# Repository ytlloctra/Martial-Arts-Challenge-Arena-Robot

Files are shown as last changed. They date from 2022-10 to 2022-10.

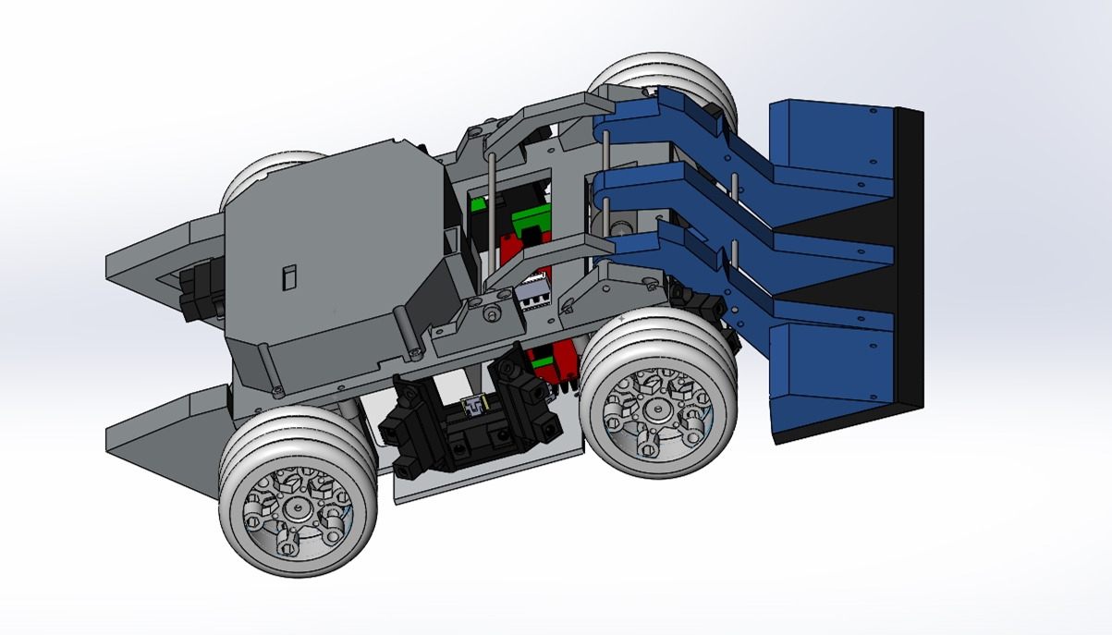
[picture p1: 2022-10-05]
3D图纸/003平铲车-改/预览图.jpg

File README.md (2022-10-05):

# 武术擂台机器人

stm32f103vet6 + oled + 得科电机 + 驼峰胎 + 红外测距传感器

## 接线

接线

传感器

Left00接PD7 

Right00接PD2

Left01接PA4

Right01接PA3

Left02接PA6

Right02接PA1

Left03接PA7

Right03接PA0

Left04接PC4

Right04接PC3 

Left05接PC5  

Right05接PC2 

Behind00接PC0

驱动板

左侧：

pwml1接PA9，pwml2接PA8，EN不接，两个GND中，只需将其中任意一个GND与主控板GND相连

右侧：

pwml1接PA11，pwml2接PA10，EN不接，两个GND中，只需将其中任意一个GND与主控板GND相连

平避障 逆时针 距离变小 顺时针 距离变大  棕正蓝负黑信号

红外测距  红正黑负黄信号

左转 左后右前  右转 左前右后

## 避障序号

避障序号

## 主要程序



```cython
void bianyuanshibie() 
{
	//int b;
if(ltsbflag==0)
{

if(hui3==1&&hui4==1&&hui1==1&&hui2==1&&mm1==1&&mm2==1)  stop();
//else ahead(300);
else if(((temp1>1700&&temp7>1700)||(temp4>1700&&temp6>1700)||(temp1>1700&&(temp4>1700||temp6>1700))||(temp7>1700&&(temp4>1700||temp6>1700))||(temp3>1700&&temp4>1700&&temp9>1700)||(temp5>1700&&temp6>1700&&temp8>1700))&&ot<3)
	{
		
			//ltsbflag=1;
					ot++;
			
	}
//else if(backflag==1&&temp1>1600) 
//{
	//if(temp1<1600) backflag=0;
	//else  stop();
//}
	
else	
{

		if(mm1==1||mm2==1||hui1==1||hui2==1)

{

	 if( temp1>1600  )    // two sensor front find enemy 2  
			{		

					if ((hui1==1||hui2==1)) 
				{
					if(temp7>1600) {left(800);x0++;}
					else	
					{
							//back(600,600);
						//if(hui1==0&&hui2==0)
						back(500,500);
						
						f++;
					}
					
				}
				
					else 
					{
						if(backflag==0)
						{
						allahead(500);
						allaheadflag=1;
						}
					}

			}
			else if(temp7>1600)  
			{
					left(800);
					x5++;
			}
		else if(  temp3>1600||temp4>1600||mm3==0||temp9>1600) //one sensor  right and right back  find enemy  and right back   2   temp3>1500 || temp4>1500  ||
			{
				
					if(temp3>1600)  right(600);
				else if(temp9>1600) right(800);
					else right(700);

			}
		else if( temp6>1600||temp5>1600||mm4==0||temp8>1600 )  //onr sensor left and left back find enemy 2    temp5>1500 ||temp6>1500 ||
			{
			
					if(temp5>1600)	left(600);
				else if(temp8>1600) left(800);
					else left(700);
				//x1++;
				
			}
		//else if(temp7>1700)  {left(720);x5++;}

		else	if(hui3==1&&hui4==1)
	{
				if(mm1==1||mm2==1||hui1==1||hui2==1)
		{
			 
				diaotou(500);x2++;
			
		}
				else
		{
		ahead(450);
		//ltsbflag=0;
		}
	}
		else 
	{
				if((hui1==1||hui2==1)&&(mm1==1||mm2==1)) {back(500,500);f++;}
				else 
				diaotou(500);
				x3++;
	}

}

else if( temp1>1600  )    // two sensor front find enemy 2  
			{		

							if(temp7>1600)  {diaotou(500);x4++;}
							else           
							{ 
						     if(backflag==0)
										{
											allahead(600);
											allaheadflag=1;
										}
							}

			}
else if(temp7>1600)  {left(900);x7++;}

else if(  temp3>1600||temp4>1600||mm3==0||temp9>1600) //one sensor  right and right back  find enemy  and right back   2   temp3>1500 || temp4>1500  ||
			{
					if(temp3>1600)  right(600);
				else if(temp9>1600) right(800);
					else right(700);
				
			}
else if( temp6>1600||temp5>1600||mm4==0||temp8>1600 )  //onr sensor left and left back find enemy 2    temp5>1500 ||temp6>1500 ||
			{
					
					if(temp5>1600)	left(600);
				else if(temp8>1600) left(800);
					else left(700);
				x6++;
			}

//else if(temp7>2000)  {left(720);x7++;}
else ahead(450);
			
}
		
}

duojiz(900);
duojiy(900);

//if(j>0&&f>0) 
	//{
 //   backflag=1;
//	}  
//	else backflag=0;
if(allaheadflag==1) 
{
	j+=4;
	if(j>300) j=300;
}
else j=0;

if(ot>2) 	{ltsbflag=1;}

}
```

## 实车



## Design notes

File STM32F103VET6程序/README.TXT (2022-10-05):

实验器材:
	MiniSTM32F103开发板V3版本
	
实验目的:
	学习定时器的PWM功能
	
硬件资源:
	1,DS0(连接在PA8) 
	2,定时器1(TIM1),使用TIM1的通道1(CH1),开启部分重映射,将TIM1_CH1输出到PA8.
	从而实现PWM输出控制DS0亮度.
	
实验现象:
	本实验,DS0由暗到亮,再由亮到暗,再由暗到亮,依次循环.
	
注意事项:
	无.  

					正点原子@ALIENTEK
					2014-3-06
					广州市星翼电子科技有限公司
					电话：020-38271790
					传真：020-36773971
					购买：http://shop62103354.taobao.com
					http://shop62057469.taobao.com
					公司网站：www.alientek.com
					技术论坛：www.openedv.com

void bianyuanshibie() 
{
	//int b;
if(ltsbflag==0)
{

if(hui3==1&&hui4==1&&hui1==1&&hui2==1&&mm1==1&&mm2==1)  stop();
//else ahead(300);
else if(((temp1>1700&&temp7>1700)||(temp4>1700&&temp6>1700)||(temp1>1700&&(temp4>1700||temp6>1700))||(temp7>1700&&(temp4>1700||temp6>1700))||(temp3>1700&&temp4>1700&&temp9>1700)||(temp5>1700&&temp6>1700&&temp8>1700))&&ot<3)
	{
		
			//ltsbflag=1;
					ot++;
			
	}
//else if(backflag==1&&temp1>1600) 
//{
	//if(temp1<1600) backflag=0;
	//else  stop();
//}
	
else	
{

		if(mm1==1||mm2==1||hui1==1||hui2==1)

{

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

		else	if(hui3==1&&hui4==1)
	{
				if(mm1==1||mm2==1||hui1==1||hui2==1)
		{
			 
				diaotou(500);x2++;
			
		}
				else
		{
		ahead(450);
		//ltsbflag=0;
		}
	}
		else 
	{
				if((hui1==1||hui2==1)&&(mm1==1||mm2==1)) {back(500,500);f++;}
				else 
				diaotou(500);
				x3++;
	}

}

else if( temp1>1600  )    // two sensor front find enemy 2  
			{		

							if(temp7>1600)  {diaotou(500);x4++;}
							else           
							{ 
						     if(backflag==0)
										{
											allahead(600);
											allaheadflag=1;
										}
							}

			}
else if(temp7>1600)  {left(900);x7++;}

else if(  temp3>1600||temp4>1600||mm3==0||temp9>1600) //one sensor  right and right back  find enemy  and right back   2   temp3>1500 || temp4>1500  ||
			{
					if(temp3>1600)  right(600);
				else if(temp9>1600) right(800);
					else right(700);
				
			}
else if( temp6>1600||temp5>1600||mm4==0||temp8>1600 )  //onr sensor left and left back find enemy 2    temp5>1500 ||temp6>1500 ||
			{
					
					if(temp5>1600)	left(600);
				else if(temp8>1600) left(800);
					else left(700);
				x6++;
			}

//else if(temp7>2000)  {left(720);x7++;}
else ahead(450);
			
}
		
}

duojiz(900);
duojiy(900);

//if(j>0&&f>0) 
	//{
 //   backflag=1;
//	}  
//	else backflag=0;
if(allaheadflag==1) 
{
	j+=4;
	if(j>300) j=300;
}
else j=0;

if(ot>2) 	{ltsbflag=1;}

}

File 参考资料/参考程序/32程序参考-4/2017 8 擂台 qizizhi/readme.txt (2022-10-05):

本实验为新建工程实验，仅供大家新建工程时参考。

	嵌入式开发网
      mcudev.taobao.com

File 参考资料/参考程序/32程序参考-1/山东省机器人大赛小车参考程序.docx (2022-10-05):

#include "delay.h"

#include "sys.h"

#include "oled.h"

#include "pwm.h"

#include "delay.h"

#include "adc.h"

#include "move.h"

#include "scan.h"

#include "buzzer.h"

//#include "usart.h"

//#include "MPU6050.h"

//#include "usmart.h"

//#include "inv_mpu.h"

#include "dma.h"

#include "timer.h"

//#include "inv_mpu_dmp_motion_driver.h"

#define TEST 0 //1为测试，0为不测试

void ltsb(void);

void delay(int t);

void TIM3_IRQHandler(void); //TIM3中断

void DMA1_Channel1_IRQHandler(void);

void bianyuanshibiex(void);

void check(void);

void show(void);

void set_num(void);

char huodejianzhi();

u8 set_led(u8 a);

extern u32 GROUP;

extern unsigned char zheng_or_fan;

extern int time;

u32 temp_z1=0,temp_z2=0,temp_z3=0,temp_z4=0,temp_z5=0,temp_z6=0,temp_y1=0,temp_y2=0,temp_y3=0,temp_y4=0,temp_y5=0,temp_y6=0,temp_Qz=0,temp_Hz=0;

u32 temp0o=0,temp1o=0,temp2o=0,temp3o=0,temp4o=0,temp5o=0,temp6o=0,temp7o=0,temp8o=0,temp9o=0,temp_left_aheado=0,temp_left_backo=0;

u8 hui1,hui2,hui3,hui4,rlfalg=1,hui5,hui6;

u8 mm1,mm2,mm3,mm4,mm5,mm6,oldmm3,oldmm4,mm7,mm8,key=0,key_flag=0;

u8 ltsbflag=0,allaheadflag=0,backflag=0,ltsbback=0,ltsbjiao=0,rightflag=0,leftflag=0,backflag1=0,backflag2=0,leitaichu=0,ltxback=0,ltxahead=0,ltsbin=0,enemyflag=0,uptai=0;

u32 xr=0,ra=0,la=0,yj=0,zj=0, t=0,ot=0,ot1=0,j=0,f=0,x=0,rf=0,lf=0,tj=0;

int x1,x2,x3,x4,x5,x6,x7,x0,sum[6]={0},mpu[6]={0},sub[6]={0},i,xj=0;

u16 value[14],y=0;

int kp=5,kd=1,lasttime=0,apwm=0,expectspeed=0,error=0,key_num=0;

u32 check45_PWM=900,check90_PWM=900,check45_TIME=100,check90_TIME=200,checkback_PWM=700,checkback_TIME=200; //check参数设置

int main(void)

{

delay_init(); //延时函数初始化

delay_ms(1000);

delay_ms(1000);

NVIC_Configuration(); //设置NVIC中断分组2:2位抢占优先级，2位响应优先级 LED_Init(); //LED端口初始化

BUZZER_GPIO_Config(); //

OLED_Init(); //初始化OLED

MYDMA_Config(DMA1_Channel1,(u32)&ADC1->DR,(u32)&value,14);//初始化DMA

Adc_Init(); //初始化ADC

TIM1_PWM_Init(1799,0); //电机PWM频率=72000/(1799+1)=40Khz

TIM4_PWM_Init(1799,0); //上台电机

TIM2_Int_Init(2499,143); //定时器

mm_scan_GPIO_Config(); //红外对管管脚初始化（普通IO输入）

TIM3_PWM_Init(359*4,0); //正交解码

while(key_flag==0) //等待手势启动

{

set_num();

logo(); //显示LOGO

}

OLED_Clear() ; //OLED 清零

/* delay_ms(500);

ahead(1300);

aheadST(1500);

delay_ms(220);

apwm=0;

TIM_SetCompare3(TIM4,0);//B8 you

TIM_SetCompare4(TIM4,0);//B9

delay_ms(700);*/

while(1)

{

#if TEST==1

{

TIM_SetCompare1(TIM1,0);//a8 x/1800

TIM_SetCompare2(TIM1,xj);//a9

TIM_SetCompare3(TIM1,0);//a10

TIM_SetCompare4(TIM1,xj);//a11

TIM_SetCompare3(TIM4,0);//a10

TIM_SetCompare4(TIM4,xj);//a11

set_num();

show();

}

#else

{

show(); //显示参数

// ltsb(); //擂台下识别

bianyuanshibiex(); //擂台上边缘识别

/*************************/

stop();

expectspeed=0;

error=expectspeed-time;

{

apwm+=kp*error+kd*(error-lasttime);

if(apwm>500) {apwm=500;}

if(apwm<-500) {apwm=-500;}

if(apwm<0) {backST(-apwm);x7=2;}

else {aheadST(apwm);;x7=1;}

}

/*************************/

lasttime=error;

if(xj/160==1) {xj=0;}

set_led(xj/20+1);

xj++;

leftflag=0;rightflag=0;backflag2=0;allaheadflag=0;ltxback=0; //flag清零

}

#endif

}

}

/******************delay 改进*********************/

/**************************************************/

void delay(int t)

{

int i;

for(i=t/1000 ; i>0 ;i-- )

{

delay_ms(1000);

}

delay_ms(t%1000);

}

/******************边缘改进*********************/

/**************************************************/

void bianyuanshibiex(void)

{

//doordown();

if(ltsbflag==0)

//if(hui3==1&&hui4==1&&hui1==1&&hui2==1&&mm1==1&&mm2==1) stop();

{ doordown();

/*if(((left1>1300&&(temp_back>1300||mm7==0||mm8==0))||(left1>1300&&(temp_back>1300||mm7==0||mm8==0))||(left1>1300&&(temp_right>1300||temp_left>1300))||((temp_back>1300||mm7==0||mm8==0)&&(temp_right>1300||temp_left>1300))||(temp_ahead_right>1300&&temp_right>1300&&temp_back_right>1300)||(temp_left>1300&&temp_ahead_left>1300&&temp_back_left>1300)))

{

//ltsbflag=1;

// ltsbin=1;

}

//else if(uptai==1){left(1000);delay_ms(200);uptai=0;}

else*/ if( temp_z1>1300 ||temp_y1>1300||temp_Qz>1300 ) // two sensor front find enemy 2

{ //ot=5;

// if((hui1==1||hui2==1)&&GROUP==1) {back(500,500);backflag=1;}

if(mm1==1||mm3==1) {back(500,500);backflag=1;}

else

{

if(backflag==1)

{

back(500,500);

delay_ms(100);

if(yj==1)

{

right(500);

}

else

{

left(500);

}

delay_ms(150);

backflag=0;

}

else allahead(500);

allaheadflag=1;

}

backflag1=0;

}

else if((mm1==1||mm3==1))

{

back(500,500);backflag1=1;xj=0;backflag=0;

}

else if( temp_z2>1300||( temp_z3>1300)||temp_z4>1300||temp_z5>1300||temp_z6>1300) //one sensor right and right back find enemy and right back 2 temp_ahead_right>1500 || temp_right>1500 ||

{

left(500);

}

else if( temp_y2>1300||( temp_y3>1300)||temp_y4>1300||temp_y5>1300||temp_y6>1300) //one sensor left and left back find enemy 2 temp_left>1500 ||temp_back>1500 ||

{ right(500);

}

else

{

backflag=0;

if(backflag1==1)

{

//back(500,500);delay_ms(100);

if(yj==1)

{

right(500);

}

else

{

left(500);

}

delay_ms(200);

backflag1=0;

}

// else if((hui1==0&&hui2==0&&hui3==0&&hui4==0)&&GROUP==1) ahead(500);//满电550

else ahead(500);

}

if(allaheadflag==1) zj++;

else zj=0;

if(ot>0) enemyflag=1;

else enemyflag=0;

if(ot<=0) ot=0;

/*if(xj==1) BUZZER(1);

else BUZZER(0);*/

duojiup();

ltxback=0;ltxahead=0;ot--;

}

}

/*****************擂台下识别********************/

/**************************************************/

/*void ltsb()

{

if(ltsbflag==1)

{ doorup();

{

if(x1>2)

{

while(value[0]>1100)

right(400);

ahead(700);

delay_ms(500);

x1=0;

}

if((left1>1500&&(mm7==0||mm8==0)&&temp_back_on<1700&&temp_left<1700&&temp_right<1700)&&ltsbback==0&&ltsbjiao==0)

{

if(t>=3)

{

back(300,300);

duojidown();

delay_ms(300);

back(600,600);

x1++;

delay_ms(1000);

delay_ms(10);

duojiup();

uptai=1;

}

t++;

}

else if((left1>1100&&temp_right>1700&&temp_right_ahead>1700))

{

ahead(400);

t=0;ltxback=1;

}

else if((left1>1100&&temp_left>1700&&temp_left_ahead>1700))

{

ahead(400);

t=0;ltxback=2;

}

else if((left1<1300&&temp_left>1300&&temp_right<1300&&temp_back<1300&&temp_back_on<1300)||(left1>1300&&temp_left<1300&&temp_right<1300&&temp_back<1300&&temp_back_on<1300)||(left1<1300&&temp_left<1300&&temp_right>1300&&temp_back<1300&&temp_back_on<1300)||(left1<1300&&temp_left<1300&&temp_right<1300&&temp_back>1300)||(left1<1300&&temp_left<1300&&temp_right<1300&&temp_back<1300&&temp_back_on<1300))

{

if(ltsbjiao==0)

{

duojiup();

t=0;

BUZZER(0);

leitaichu++;

}

}

else

{

{

if(ltxback==1) right(400);

else left(400);

ltsbback=0;

}

duojiup();

t=0;

ltsbjiao=0;

}

if(t>0&&t<4)

{

if( temp_back_on>1700&&t<3) {ltxback=3;t=0;}

else if(t>1&&t<3)

{back(300,300);

delay_ms(400);}

}

else t=0;

if(leitaichu>1)

{

leitaichu=0;

ltsbflag=0;

}

if(ltxback==1||ltxback==2) tj++;

else tj=0;

if(tj>100)

{

if(ltxback==2)

{

back(500,500);

delay_ms(100);

while(value[0]>1100) right(400);

ahead(700);

delay_ms(1000);

left(700);

delay_ms(300);

tj=0;

}

else if(ltxback==1)

{

back(500,500);

delay_ms(100);

while(value[0]>1100) left(400);

ahead(700);

delay_ms(1000);

right(700);

delay_ms(300);

tj=0;

}

}

if(ltxback==3)

{

if(mm7==0) while(value[0]>1100) left(400);

else while(value[0]>1100) right(400);

ahead(700);

delay_ms(500);

}

}

}

}*/

/****************显示与检测**************************/

/*********************************************/

void show()

{

temp_z1=value[5];//

temp_z2=value[4];//

temp_z3=value[3];//

temp_z4=value[2];//

temp_z5=value[1];//

temp_z6=value[0];//

temp_y1=value[6];//

temp_y2=value[7];//

temp_y3=value[8];//

temp_y4=value[9];//

temp_y5=value[10];//

temp_y6=value[11];//

temp_Qz=value[13];//

temp_Hz=value[12];//

/* mm3=mm_scan(GPIOC,GPIO_Pin_3); // 右下 C3 左5

mm4=mm_scan(GPIOC,GPIO_Pin_1); // 左下 C1 左6

mm5=mm_scan(GPIOD,GPIO_Pin_1);//默认是低 所以是下拉 下前左 D1

mm6=mm_scan(GPIOD,GPIO_Pin_3); // 下前右 D3

hui3=mm_scan(GPIOD,GPIO_Pin_5); // 下后左 D5

hui4=mm_scan(GPIOD,GPIO_Pin_7); // 下后右 D7

mm1=mm_scan(GPIOA,GPIO_Pin_13); // 默认是高 所以是上拉 右上 A13

mm2=mm_scan(GPIOA,GPIO_Pin_15); // 左上 A15*/

// hui3=mm_scan(GPIOA,GPIO_Pin_13); //默认是低 所以是下拉 下后左 D6

// hui4=mm_scan(GPIOA,GPIO_Pin_15); // 下后右 D7

mm1=mm_scan(GPIOD,GPIO_Pin_7);//

mm2=mm_scan(GPIOD,GPIO_Pin_6);

mm3=mm_scan(GPIOD,GPIO_Pin_2);

mm4=mm_scan(GPIOD,GPIO_Pin_1);

/* if(temp_z1>1300) OLED_ShowNum(0,0,temp_z1,4,12);

else OLED_ShowNum(0,0,0,4,12);

if(temp_z2>1300) OLED_ShowNum(0,2,temp_z2,4,12);

else OLED_ShowNum(0,2,0,4,12);

if(temp_z3>1300) OLED_ShowNum(0,4,temp_z3,4,12);

else OLED_ShowNum(0,4,0,4,12);

if(temp_z4>1300) OLED_ShowNum(0,6,temp_z4,4,12);

else OLED_ShowNum(0,6,0,4,12);

if(temp_z5>1300) OLED_ShowNum(26,2,temp_z5,4,12);

else OLED_ShowNum(26,2,0,4,12);

if(temp_z6>1100) OLED_ShowNum(26,4, temp_z6,4,12);

else OLED_ShowNum(26,4, 0,4,12);

if(temp_y1>1300) OLED_ShowNum(78,0,temp_y1,4,12);

else OLED_ShowNum(78,0,0,4,12);

if(temp_y2>1300) OLED_ShowNum(78,2,temp_y2,4,12);

else OLED_ShowNum(78,2,0,4,12);

if(temp_y3>1300) OLED_ShowNum(78,4,temp_y3,4,12);

else OLED_ShowNum(78,4,0,4,12);

if(temp_y4>1300) OLED_ShowNum(78,6,temp_y4,4,12);

else OLED_ShowNum(78,6,0,4,12);

if(temp_y5>1300) OLED_ShowNum(52,2,temp_y5,4,12);

else OLED_ShowNum(52,2,0,4,12);

if(temp_y6>1300) OLED_ShowNum(52,4,temp_y6,4,12);

else OLED_ShowNum(52,4,0,4,12);

if(temp_Qz>1300) OLED_ShowNum(39,0,temp_Qz,4,12);

else OLED_ShowNum(39,0,0,4,12);

if(temp_Hz>1300) OLED_ShowNum(39,6,temp_Hz,4,12);

else OLED_ShowNum(39,6,0,4,12); */

if(apwm<0) OLED_ShowNum(0,0,2,4,12);

else OLED_ShowNum(0,0,1,4,12);

OLED_ShowNum(26,0,abs(apwm),4,12);

if(time<0) OLED_ShowNum(0,2,2,4,12);

else OLED_ShowNum(0,2,1,4,12);

OLED_ShowNum(26,2,abs(time),4,12);

if(error<0) OLED_ShowNum(0,4,2,4,12);

else OLED_ShowNum(0,4,1,4,12);

OLED_ShowNum(26,4,abs(error),4,12);

OLED_ShowNum(52,0,x7,1,12);

// OLED_ShowNum(104,4,mm4,1,5);

OLED_ShowNum(0,6,zheng_or_fan,1,5);

}

char huodejianzhi()

{ //1 left 2 right 3 up 4 down 5 mid

u8 key_l=0,key_r=0,key_up=0,key_down=0,key_mid=0;

key_l=key_get(GPIOC,GPIO_Pin_6); //d13

key_r=key_get(GPIOD,GPIO_Pin_13); //d12

key_up=key_get(GPIOD,GPIO_Pin_12); //c6

key_down=key_get(GPIOD,GPIO_Pin_14); //d15

key_mid=key_get(GPIOD,GPIO_Pin_15); //d14

//OLED_Clear() ;

/* OLED_ShowNum(0,2,key_l,4,12);

OLED_ShowNum(52,2,key_r,4,12);

OLED_ShowNum(26,0,key_up,4,12);

OLED_ShowNum(26,4,key_down,4,12);

OLED_ShowNum(26,2,key_mid,4,12);*/

if(key_l == 1) //left

{

key=1;

}

if(key_r == 1) //right

{

{key=2;

}

}

if(key_up == 1) //up

{

{key=3;

}

}

if(key_down == 1) //down

{

{key=4;

}

}

if(key_mid == 1) //mid

{

{key=5;

}

}

return key; }

void set_num()

{

switch(huodejianzhi())//key

{

case 5: //mid

{

key=0;

delay_ms(150);

if(key_flag==1)

{

key_flag=0;

}

else if(key_flag==0)

{

key_flag=1;

}

delay_ms(150);

//xj-=1;

} break;

default: break;

case 4: //down

{

key=0;

delay_ms(120);

xj-=1;

delay_ms(120);

} break;

case 3: //up

{

key=0;

delay_ms(120);

xj+=1;

delay_ms(120);

}break;

case 2: //right

if(key_num==0)

{

key=0;

delay_ms(120);

xj+=50;

delay_ms(120);

}

/* else if(key_num==1)

{

key=0;

delay_ms(120);

expect_Speed_Min-=3;

delay_ms(120);

}

else if(key_num==2)

{

key=0;

delay_ms(120);

slow1-=3;

delay_ms(120);

}

else if(key_num==3)

{

key=0;

delay_ms(120);

eKP-=20;

delay_ms(120);

}

else if(key_num==4)

{

key=0;

delay_ms(120);

KD-=10;

delay_ms(120);

}

else if(key_num==5)

{

key=0;

delay_ms(120);

SpeedKP-=1;

delay_ms(120);

}

else if(key_num==6)

{

key=0;

delay_ms(120);

SpeedKI-=5;

delay_ms(120);

}

else if(key_num==7)

{

key=0;

delay_ms(120);

SpeedKD-=1;

delay_ms(120);

}*/

break;

case 1: //left

if(key_num==0)

{

key=0;

delay_ms(120);

xj-=50;

delay_ms(120);

}

/* else if(key_num==1)

{

key=0;

delay_ms(120);

expect_Speed_Min+=3;

delay_ms(120);

}

else if(key_num==2)

{

key=0;

delay_ms(120);

slow1+=3;

delay_ms(120);

}

else if(key_num==3)

{

key=0;

delay_ms(120);

eKP+=20;

delay_ms(120);

}

else if(key_num==4)

{

key=0;

delay_ms(120);

KD+=10;

delay_ms(120);

}

else if(key_num==5)

{

key=0;

delay_ms(120);

SpeedKP+=1;

delay_ms(120);

}

else if(key_num==6)

{

key=0;

delay_ms(120);

SpeedKI+=5;

delay_ms(120);

}

else if(key_num==7)

{

key=0;

delay_ms(120);

SpeedKD+=1;

delay_ms(120);

}*/

break;

}

}

u8 set_led(u8 a)

{

switch(a)

{

case 1:

GPIO_ResetBits(GPIOD,GPIO_Pin_11); //a

GPIO_ResetBits(GPIOD,GPIO_Pin_10); //b

GPIO_ResetBits(GPIOD,GPIO_Pin_9); //c

break;

case 2:

GPIO_SetBits(GPIOD,GPIO_Pin_11); //a

GPIO_ResetBits(GPIOD,GPIO_Pin_10); //b

GPIO_ResetBits(GPIOD,GPIO_Pin_9); //c

break;

case 3:

GPIO_ResetBits(GPIOD,GPIO_Pin_11); //a

GPIO_SetBits(GPIOD,GPIO_Pin_10); //b

GPIO_ResetBits(GPIOD,GPIO_Pin_9); //c

break;

case 4:

GPIO_SetBits(GPIOD,GPIO_Pin_11); //a

GPIO_SetBits(GPIOD,GPIO_Pin_10); //b

GPIO_ResetBits(GPIOD,GPIO_Pin_9); //c

break;

case 5:

GPIO_ResetBits(GPIOD,GPIO_Pin_11); //a

GPIO_ResetBits(GPIOD,GPIO_Pin_10); //b

GPIO_SetBits(GPIOD,GPIO_Pin_9); //c

break;

case 6:

GPIO_SetBits(GPIOD,GPIO_Pin_11); //a

GPIO_ResetBits(GPIOD,GPIO_Pin_10); //b

GPIO_SetBits(GPIOD,GPIO_Pin_9); //c

break;

case 7:

GPIO_ResetBits(GPIOD,GPIO_Pin_11); //a

GPIO_SetBits(GPIOD,GPIO_Pin_10); //b

GPIO_SetBits(GPIOD,GPIO_Pin_9); //c

break;

case 8:

GPIO_SetBits(GPIOD,GPIO_Pin_11); //a

GPIO_SetBits(GPIOD,GPIO_Pin_10); //b

GPIO_SetBits(GPIOD,GPIO_Pin_9); //c

break;

}

return 0;

}

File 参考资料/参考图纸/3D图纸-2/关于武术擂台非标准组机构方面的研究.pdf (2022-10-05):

## 关于武术擂台非标准组机构方面的研究

内蒙古民族大学

## 张凌峰 一、车体

作为一个对抗类别的机器人，谈其稳定性是很有必要的。一个好的车体结构，不仅可以

降低重心使车体稳定，更能增加转向灵活性，侧滑抗性。有些人会觉得一个车体不就是一个

板子加四个电机和车轮而已嘛，提出这些疑惑的人要么没玩过这个，要么玩过也没成绩。其

实这里面也有一些文章。

1.车体要做到尽量的大，比赛方给定的 300*300 投影面积我们不要嫌多，充分利用好

这宝贵的 300*300。大的好处不用多说，有充足的空间安放电池、传感器等电子器件，更

大的底盘可以让车的轴距和轮距更大，加强车体稳定性，增加侧滑抗性。

2.车的四个轮子与地面的切点位置要尽量做成正方形，或者长大于高的矩形，这样有助

于增加车的灵活性，这是因为多数车（至少是本人目力所及）转向是靠差速转向。有些人喜

欢做成六个轮子的车，这样牺牲了灵活性，换区了更大的抓地力，这个问题没有孰强孰弱之

分，大家见仁见智。

3.车体结构要便于拆装，以便调节或更换传感器等电子器件。无论比赛还是日常调试，

元器件损坏都是再正常不过的事情了，一个好的车体能够节省很多维护维修时间。我大学期

间参加比赛时候，我小伙伴就被坑过，调试一次传感器就要把整个车都拆了。当然那种东西

肯定不是我设计的。

4.尽量把电池放在最下面，并且便于拆装。车体很大一部分重量都是电池，一块 6s 的

2000~3000 毫安的航模电池就要 290g~350g 左右，这对于全车 4kg 来说是很大一部分比

重。放在下面可以有效降低重心，增加稳定性。因为车重的限制我们不可能放置大容量的电

池，但在比赛期间是允许更换电池的，所以电池要便于拆装。

5.坚固与重量平衡。这个不用多说，保护传感器的东西不坚固后果谁都知道，本人亲自

吃过这个亏。如果读者感到很迷茫，在这里我推荐大家用 6 系铝合金或者碳纤维，既保证

其刚度强度，又不浪费重量，因为限制重量真是个让人头疼的问题。 二、铲子

比赛是不对进攻形式做限制的，但要保证不能对人产生伤害。无论是扔出去也好，像斗

牛士一样把对手耍下去也好，这些都不如把对手推下去直接。我曾经见过一辆车，上面举了

两个白旗，先不讨论画面滑稽与否，单是其创意就值得我们学习。白旗的目的是干扰敌人传

感器识别，让其误判断，迷惑对手，引诱对手下台。整场比赛下来也只成功了一次，而其自

身是没有丝毫攻击性的，这样的被动方式铸就了失败的必然。所以用铲子将对手像垃圾推下

台去是最直接有效的。

1.铲子形状。经事实证明，一个平的，紧贴合地面的铲子是要优越于尖的所谓的“冲角”

的。铲子与地面的交线尽量的长，这样做的好处从概率来讲就是增加攻击的准确率。铲子与

地面交线处一定要打磨平整，用油石打磨出一个刃，你要说非要用外圆磨床打磨，我只能说

土豪我们做朋友吧。

2.铲子的角度。一般取 20 度~45 度之间。

3.传感器孔。在保证刚度的情况下尽可能的大。因为车在巡航和攻击的时候，因为铲子

与车体非刚性配合，势必会发生抖动，一个与传感器视野“完美无缺”的孔在抖动时或多或

少会影响到传感器。

4.铲子支撑点的选择。这一点我要着重讲述，一个好的支撑点可以避免与你配置差不多

的车胶着，因为你可以干翻他。当然前提是你们双方的车谁也没把谁铲起，只是在拼蛮力。

当你的铲子受力时，铲子支撑点高度水平线处会与后轮与地面交点处的力，使车有轴向方向

转动的趋势，造成的结果就是前轮抬起，车子抓地力下降，有力气用不上。而支撑点越低，

这个力矩的力臂就越短，受到的力是恒定的，前车轮抬起的幅度或趋势就会下降或消失，这

样能充分发挥车辆性能，保证抓地力稳定。当然一个合理的铲子限位也能解决这个问题，前

提是合理，限位问题我在后文会提及。 三、传感器支架

1.模块化。模块化的传感器安装方便，易于在损坏的时候更换。

2.一定的偏斜角度。受限于某些传感器机理（例如漫反射光电开关），我们不可能将两

个平行的传感器并排使用，适当的给予 2 度~3 度的夹角效果会更好。这样虽然会增加一丝

丝盲区，但对于传感器的稳定来说，这点牺牲是值得的。 四、轮毂

如果直接自己制作轮毂的同学可以略过本小结，上网购买φ67 的驼峰胎的同学还是看

看吧。

1.径向加固。Φ67 的驼峰胎的轮毂可以说是非常脆弱，我不清楚设计者这样设计是为

了什么，或者说它根本不是为了这项比赛而设计的。这时我们需要径向加固，幸运的是轮毂

上有螺丝孔位，我们只需要一个带有对应孔位的内部有合适的六边形的钢片既可以加固。

2.轴向加固。这个不需要解释太多，10.9 级螺丝加垫片加弹簧垫片。 五、限位装置

一个好的限位装置能够让你的车在擂台上如鱼得水、进退自如；而一个愚蠢的限位装置

能让你在准备阶段手忙脚乱，在擂台上自缚手脚。所以说合理的限位装置还是很必要的。

1.机械类限位装置。无论是铰链自锁、弹簧挂钩、弹性钢片等等，都属于这个范畴。这

样的装置结构简单，造价低廉，但其暴露出来的问题也是致命的。这种放式一旦锁死就无法

自动解开，在你与敌人对撞失利的时候（铲子被别人铲起来），车轮会因为愚蠢的限位而与

地面的正压力下降，减小与地面的摩擦力，甚至会离开地面。另一方面在准备阶段你要手动

去解锁的你每一个铲子的限位装置，很浪费时间。

2.电磁铁类限位装置。电磁铁的优点是开合自如，通电锁死，断电松开。想象一下配合

陀螺仪的使用，当你的车在失利的情况下也会有机会逃脱追击，杀个回马枪。 六、创新想法

我在大一的时候，也有过各种不切合实际的想法。什么喷盐水呀，喷碳粉呀，电火花打

火脉冲干扰呀等等，除了违反比赛规则就是违反比赛规则。抛开那些不切合实际的想法，还

是有一些能够使用的，我会在下面一一列出。

1.隐形装置。绝大多数擂台车都是利用光学传感器探测敌人，而一个角度在 45 度以下

的镜面会完全反射光，利用这一点可以做到车体隐形。我曾经亲自设计过一辆这种类型的车，

碍于自重的原因无法实现。推荐材料 8k 镜面不锈钢。

2.涵道装置。航模界的电涵道的推力大家是都知道的，不知道可以联想战斗机引擎。我

曾经见到过用过这玩意的车，它在上方安置一涵道，向上吹高速气流，其目的是增加车与地

面的正压力。但其底盘是没有开孔的，气流从侧面进入，上方喷出，我观察过他们的测试结

果，可以增加车重 4kg 左右，效果十分明显，而且因为陀螺效应，车体十分稳定，应该说

是万分稳定。但其缺点也是十分明显的，高速转动的叶轮不仅十分危险，而且电机的耗电量

也是惊人的。

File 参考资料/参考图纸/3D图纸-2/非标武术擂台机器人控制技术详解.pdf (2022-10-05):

# 非标武术擂台机器人控制技术详解By赵晓伟

写在前面，外面的世界很大，擂台赛只是个很基础很简单的比赛，基本的纯开环就可以跑的很好，基本不需要任何控制算法，简单来说，这个 比赛是个很low很低端的比赛，不要觉得在自治区无敌，就是真的无敌了，这个比赛，对于较为优秀的学校来说，只是给大一学生用来练手，为 参加robomasters或者robocon做初期入门的，在自治区无敌，只是因为自治区水平太渣，而不是我们把擂台车这一比赛做到了极致，有没有做 到极致，看看糟乱的电路，扩了一遍又一遍的孔，其实就知道了。希望后来人，以做产品的思维来做比赛，真正能从这个比赛中学到知识，比 如传感器滤波算法设计，实时性程序架构设计等。而不是一年又一年的焊板子，拧螺丝。

## 物体检测传感器方案选择

### 可选择的传感器有以下几种

声呐传感器
声呐传感器的原理如下：发出1ms的超声波，频率从50hz～250khz，记录声呐信号从发出到被接受所用的时间。测得的飞越时间正比于离传感 器圆锥上最近障碍物距离的2倍，如果一定时间内没有收到任何信号，则说明相应的距离内没有检测到的障碍物。 声呐传感器有很多的缺点，但仍不失为是一种有用的传感器系统，同时有大量如何解决这些缺点的文章，声呐传感器最为显著的问题时反射和 干扰。当声音信号反射时，假如以一定的角度从墙面反射，则从测量结果得出的障碍物距离比实际要远得多，如果有几个声呐传感器同时工 作，就会发生干扰。
激光传感器
在很多移动机器人平台中，声呐传感器已经被红外传感器或者激光传感器所取代，不过主要应用在slam方向，对于擂台机器人的4KG平台来 说，重量比较高，而且高度以及设计中保护传感器等比较难。
红外传感器
由于光子的飞越时间对于简单而廉价的传感器阵列来说太短了，因此红外测距传感器不能采用与声呐传感器相同的方法，取而代之的是，红外 （IR）传感器通常 使用频率在40khz左右的脉冲的红外led以及一个检测而阵列，反射光线的相角随着目标的变化而变化，这样就可以来测 量距离。使用的波长一般是880nm，尽管人眼不可见，但是红外检测卡或者红外摄像机（IR-sensitive camera)将光束捕获后，转化为可见光。 红外接近开关
红外接近开关（IR proximity switches）本质上比红外psd更为简单，相当于接触式二进制传感器，只可以返回或1。 目前常用的传感器方案有以下俩种

### 第一种方案 光电开关用做距离检测传感器

使用光电开关作为距离检测传感器主要有着以下优点
数字量便于处理
数字量相对于模拟量来说抗干扰性较强
同时使用光电开关作为距离检测传感器存在许多缺陷
检测距离固定，灵活性差
受限于传感器原理，强光以前深色物体对传感器距离检测影响较大 传感器时序时间为2ms对于编程人员来说，容易造成数据丢失现象，在实际使用中会出现检测不到其他擂台车的情况

### 第二种方案使用红外测距传感器作为距离检测传感器

使用该传感器主要有以下优点
数据为模拟量，信息丰富，便于处理以及设计算法
测距时序40ms，不会丢失任何数据
颜色以及光线不会对传感器距离检测造成影响，可以保证返回准确的测距信息 当然该传感器也会由于使用者能力不足而产生许多问题
控制器设计时模数隔离设计缺陷导致ADC基准电压波动而使测距出现偏差 由于使用者能力不足而无法准确处理传感器数据，甚至无法实现基本功能 没有能力设计合理的传感器数字滤波算法

## 边缘检测传感器方案选择

对于边缘检测来说，目前也基本上有以下二种选择方案

### 第一种使用光电开关作为边缘检测传感器

这种方案相对来说数据较好处理，在前几年的擂台车比赛中出现频率较高，但是强光对其影响较大，所以在比赛中较为吃亏，仅可作为一种辅 助检测手段。并且该传感器尺寸一般为圆柱状，在激烈的比赛中很难有合适的结构为这种传感器做充足的保护。

### 第二种使用带有强光的灰度传感器作为边缘检测传感器

灰度传感器电路原理简单，可以自行设计电路，设计成模拟量传感器后，在比赛中结合一定的人机交互界面，可以做到随时修改阈值，可以依 据不同的环境影响设计不同的参数，大大提高整车运行的稳定性。

## 电机、电机驱动选型

在电机和驱动的选型中，要将其放在一个整体工程中考虑，综合考虑重量4KG，空间30*30投影等问题。 电机尽量选择连续扭矩较大的，驱动选型一定要考虑到激烈的比赛中快速换向产生的大电流，选择尺寸和额定电流较为合适的。 驱动最好做好电气隔离，或者在自行设计的控制器上面多多考虑模数隔离的问题。

## 电池选型

电池以航模电池和18650动力电池组为主，根据经验，6s 2200-3300mah尺寸和重量较为合适。 18650动力电池组记得一定要加保护板。

## 人机交互调参系统搭建

人机交互调参系统可以说时该比赛中的一个非常重要的部分，有一个合适的调参系统可以大大减少比赛中出现意外而受限于规则无法修改程序 而造成遗憾。
甚至可以设计多套程序 启动时使用人机交互界面进行引导。

## 远程调试系统搭建

对于本比赛来说，核心算法，逻辑功能可以说是万年不变的，需要调试的部分只是不同的运动姿态所对应的电机速度。 所以设计一个合理的上位机调试系统，在调试整车时，会起到事半功倍的效果，设计上位机推荐使用QT，快速简单。

## 结合基于惯性导航系统的姿态解算实现擂台车进阶功能

以下是我准备写的毕业论文的一部分，虽然是基于多旋翼平台的，但是用在擂台车上也完全可以。 惯性导航系统一般通过陀螺仪、加速度计等惯性测量元件来采集测量数据,并且解算出当前时刻的载体姿态、速度、位置等量的估算值,而且它还 能够全面的连续给出载体的位置、速率、及姿态等数据信息。另外,惯性导航系统提供的数据不仅短期精度可靠,而且它的动态特性和稳定性很 好。因此,作为惯性导航系统的一个重要的研究方向的捷联惯导系统,由于它较强的抗干扰性特点,隐蔽性,自主性和较高的数据更新率,使得它被大 量的应用于军事和民用领域。
当我们获取了当前平台的姿态 速度等信息，通过设计一系列算法，就可以避免在比赛中出现势均力敌、或者出现被铲子被铲起时，反而后退等 情况。

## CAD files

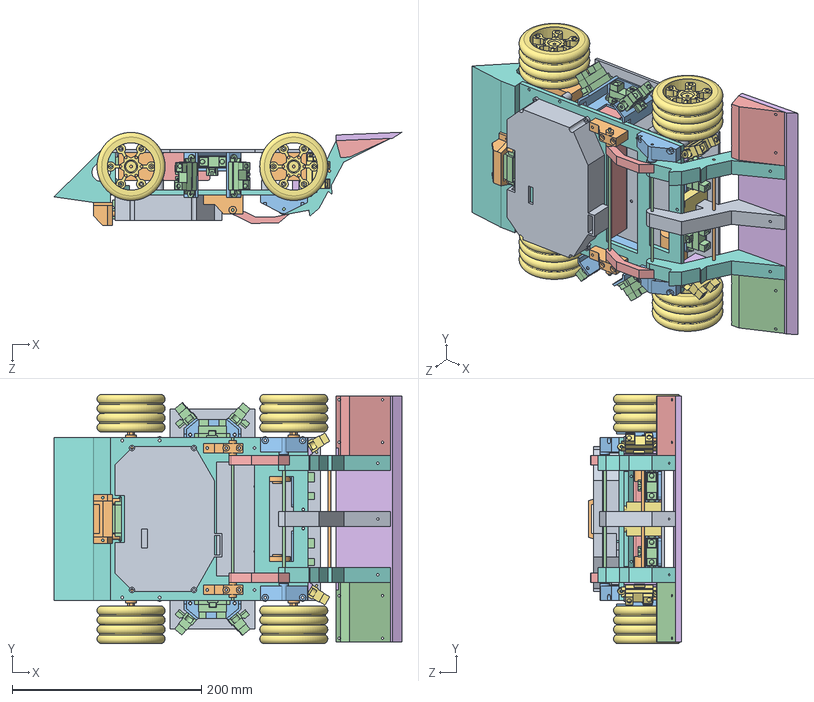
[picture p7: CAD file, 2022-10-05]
3D图纸/003平铲车-改/装配体/装配体.SLDASM
367.7 x 263.5 x 98.8 mm
底板
电机 x 4
前侧方支架 x 4
红外传感器 x 11
电池
联轴器 x 4
轮子 x 8
顶板
10mm加高支座 x 6
棘轮支座 x 2
铲子臂支座 x 2
m3 172 x 2
棘轮勾 x 2
铲底
铲子限位（车架座）
平铲臂 x 2
中间臂+限位臂
m3 134
灰度传感器 x 2
灰度保护罩右
灰度保护罩左
前侧方红外支架 x 2
裁剪红外传感器 x 2
尾撞
主控盒子
尾顶传感器支架
侧红外支架（3） x 2

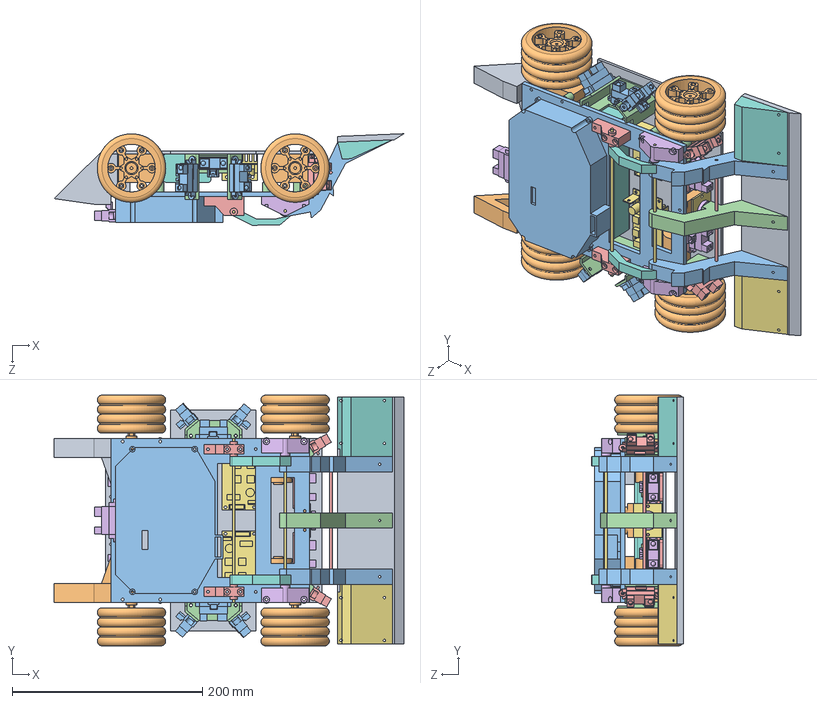
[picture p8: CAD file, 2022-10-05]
3D图纸/003平铲车/装配体/装配体.SLDASM
367.7 x 263.5 x 96.3 mm
底板
电机 x 4
红外测距传感器 x 6
新侧方测距支架 x 2
前侧方支架 x 4
红外传感器 x 5
驱动 x 2
电池
联轴器 x 4
轮子 x 8
顶板
10mm加高支座 x 6
棘轮支座 x 2
铲子臂支座 x 2
m3 172 x 2
棘轮勾 x 2
铲底
铲子限位（车架座）
平铲臂 x 2
中间臂+限位臂
m3 134
灰度传感器 x 2
灰度保护罩右
灰度保护罩左
尾撞肋
尾撞肋右1
主控盒子
前侧方红外支架 x 2
裁剪红外传感器 x 2
强磁铁 x 2
磁铁间铁板，增强磁力

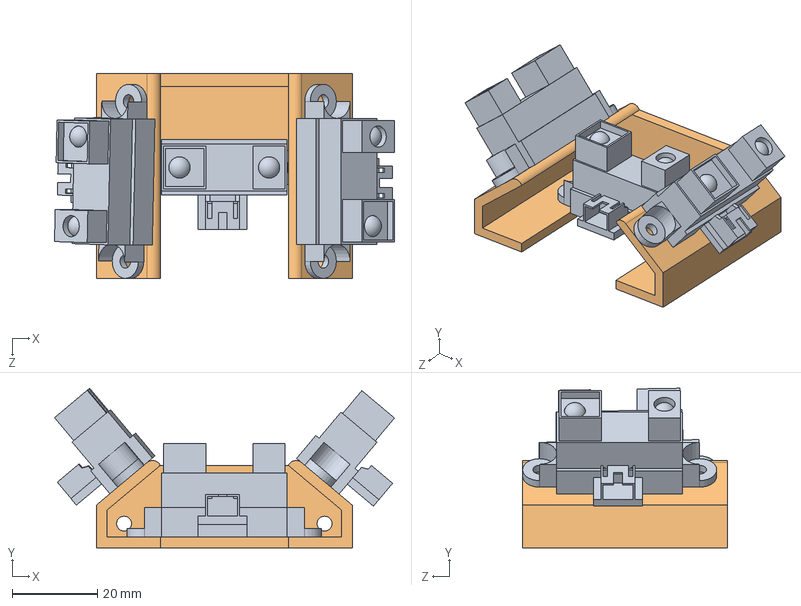
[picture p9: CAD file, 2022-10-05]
3D图纸/003平铲车/零件/侧红外组合.SLDASM
79.7 x 37.4 x 48.0 mm
红外测距传感器 x 3
新侧方测距支架

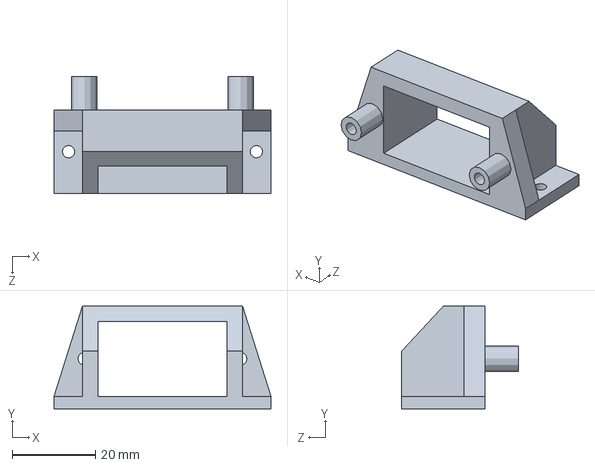
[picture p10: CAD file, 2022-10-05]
3D图纸/003平铲车-改/零件/尾顶传感器支架.SLDPRT
52.0 x 24.6 x 28.0 mm

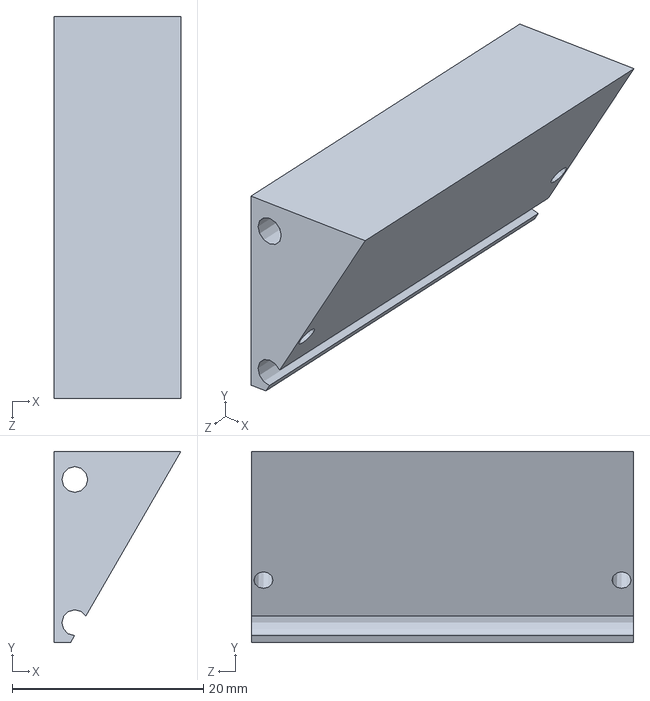
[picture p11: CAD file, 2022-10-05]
3D图纸/003平铲车/零件/铲斜红外架.SLDPRT
13.3 x 20.0 x 40.0 mm

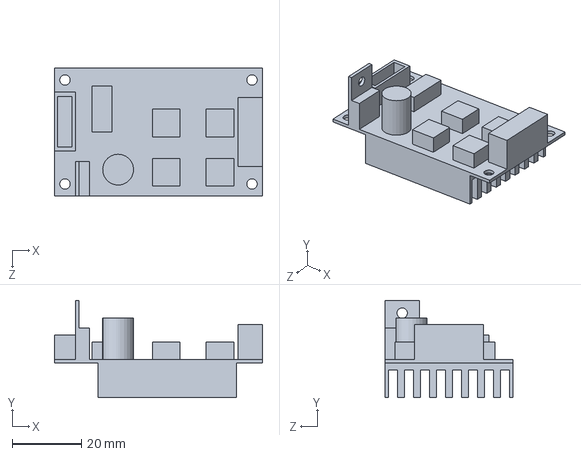
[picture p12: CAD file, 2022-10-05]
3D图纸/003平铲车-改/零件/驱动.SLDPRT
60.0 x 28.0 x 37.0 mm

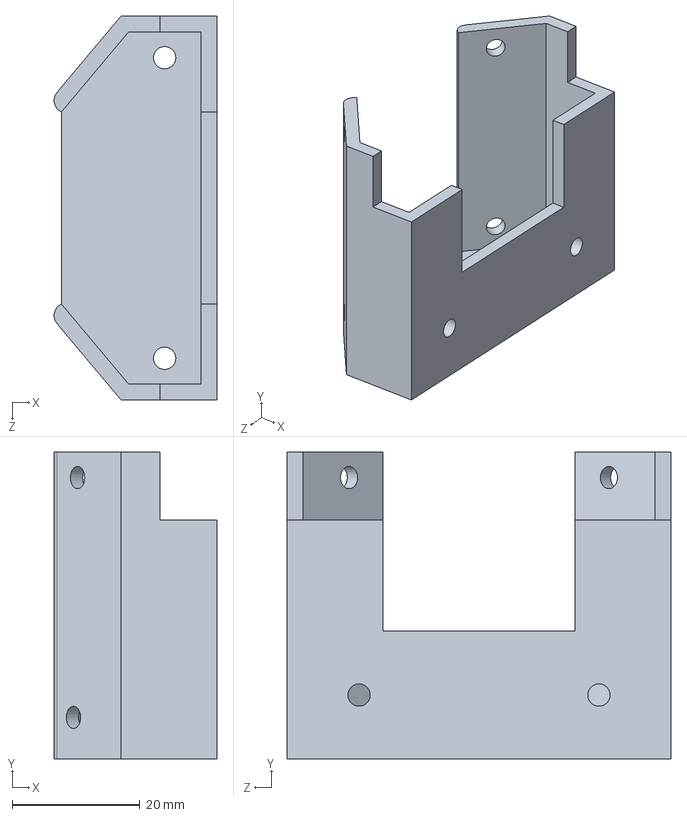
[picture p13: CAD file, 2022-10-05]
3D图纸/003平铲车/零件/侧红外支架（3）.SLDPRT
25.5 x 48.0 x 60.0 mm

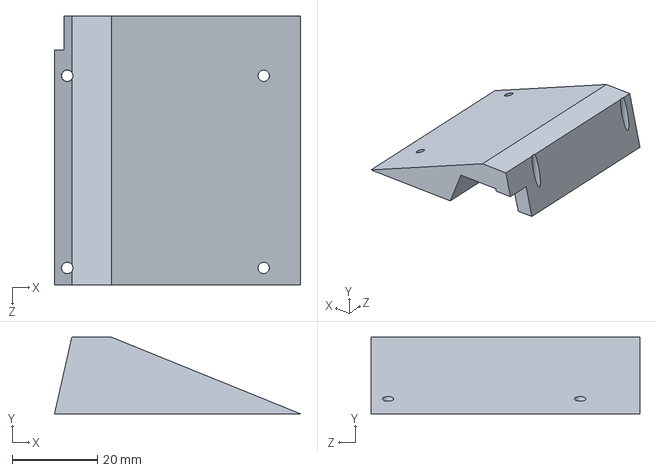
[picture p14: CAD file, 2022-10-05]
3D图纸/003平铲车-改/零件/灰度保护罩右.SLDPRT
57.6 x 18.0 x 63.0 mm

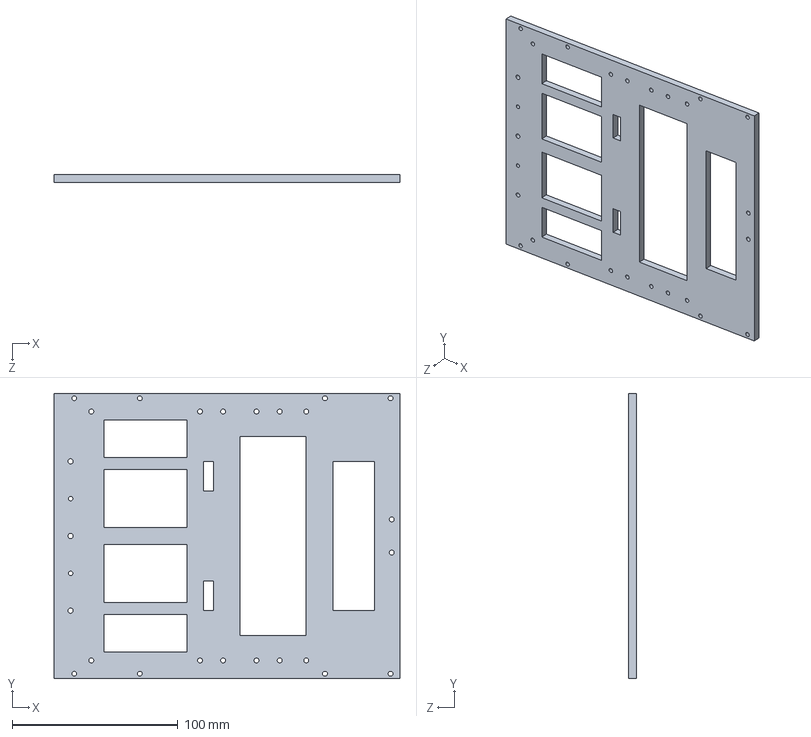
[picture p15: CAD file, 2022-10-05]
3D图纸/003平铲车/零件/顶板.SLDPRT
208.5 x 172.0 x 5.00 mm

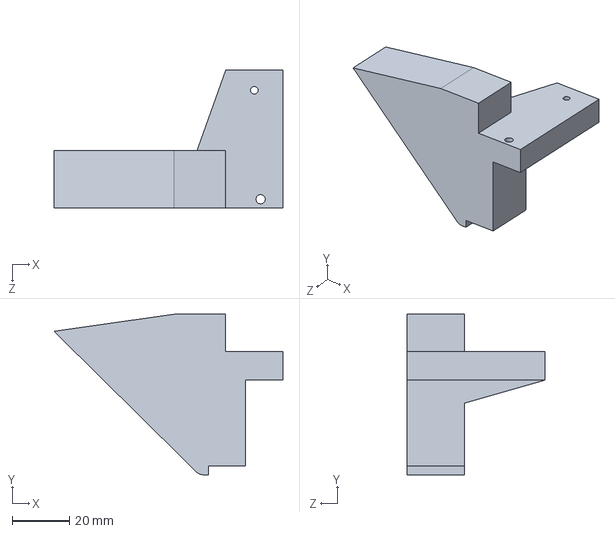
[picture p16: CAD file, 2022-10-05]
3D图纸/003平铲车/零件/尾撞肋右1.SLDPRT
79.9 x 56.0 x 48.0 mm

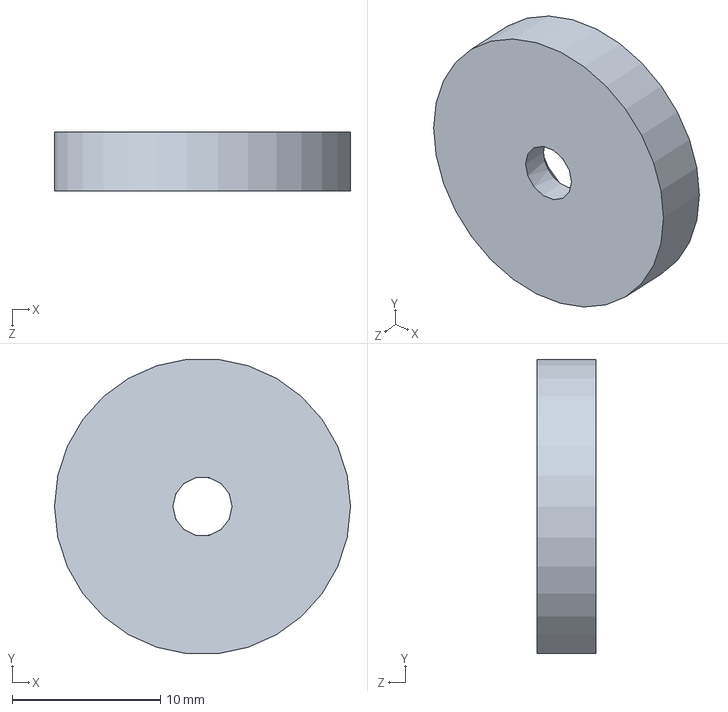
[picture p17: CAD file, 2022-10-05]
3D图纸/003平铲车-改/零件/强磁铁.SLDPRT
20.0 x 19.9 x 4.00 mm

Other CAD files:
参考资料/资料 文档/中景园电子0.96OLED显示屏资料/04-程序源码/中景园IIC接口显示屏例程/51例程/04-中景园电子0.96OLED显示屏_STC89C52系列_IIC_例程/main.OBJ
3D图纸/003平铲车-改/零件/侧红外组合.SLDASM
3D图纸/003平铲车-改/CAD图/三视图.DWG
3D图纸/003平铲车/CAD图/三视图.DWG
参考资料/资料 文档/中景园电子0.96OLED显示屏资料/04-程序源码/中景园IIC接口显示屏例程/51例程/04-中景园电子0.96OLED显示屏_STC89C52系列_IIC_例程/oled.obj
参考资料/资料 文档/中景园电子0.96OLED显示屏资料/04-程序源码/中景园IIC接口显示屏例程/51例程/04-中景园电子0.96OLED显示屏_STC89C52系列_IIC_例程/STARTUP.OBJ
3D图纸/003平铲车-改/零件/10mm加高支座.SLDPRT
3D图纸/003平铲车-改/零件/m3 134.SLDPRT
3D图纸/003平铲车-改/零件/m3 172.SLDPRT
3D图纸/003平铲车-改/零件/中间臂+限位臂.SLDPRT
3D图纸/003平铲车-改/零件/主控盒子.SLDPRT
3D图纸/003平铲车-改/零件/前侧方支架.SLDPRT
3D图纸/003平铲车-改/零件/前侧方红外支架.SLDPRT
3D图纸/003平铲车-改/零件/尾撞.SLDPRT
3D图纸/003平铲车-改/零件/尾撞肋.SLDPRT
3D图纸/003平铲车-改/零件/尾撞肋右.SLDPRT
3D图纸/003平铲车-改/零件/平铲臂.SLDPRT
3D图纸/003平铲车-改/零件/底板.SLDPRT
3D图纸/003平铲车-改/零件/棘轮勾.SLDPRT
3D图纸/003平铲车-改/零件/棘轮支座.SLDPRT
3D图纸/003平铲车-改/零件/灰度传感器.SLDPRT
3D图纸/003平铲车-改/零件/灰度保护罩左.SLDPRT
3D图纸/003平铲车-改/零件/电机.SLDPRT
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

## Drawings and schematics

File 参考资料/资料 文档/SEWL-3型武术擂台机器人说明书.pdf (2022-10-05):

# 天津赛思恩科技有限公司武术擂台机器 人使用说明书

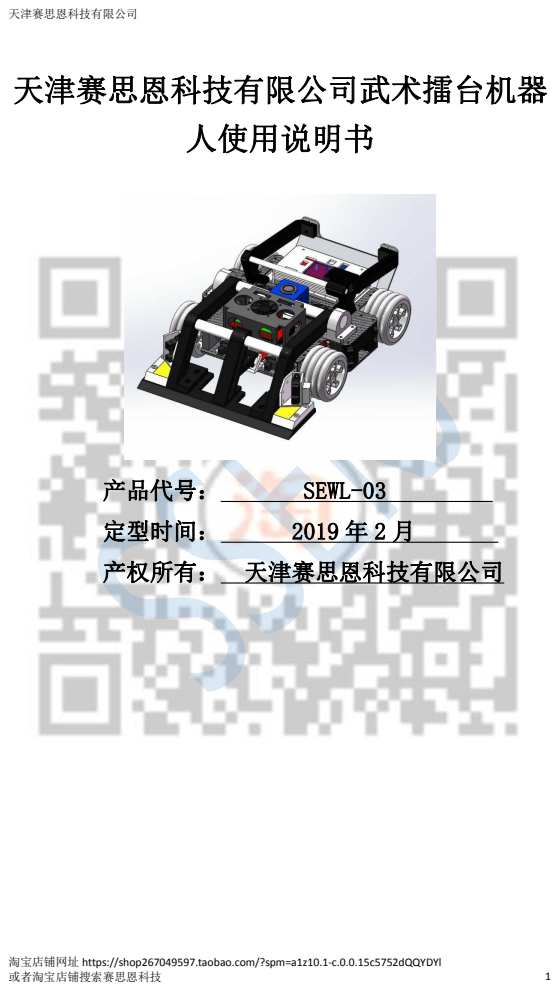
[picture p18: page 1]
天津赛思恩科技有限公司; 或者淘宝店铺搜索赛思恩科技; 产品代号：; SEWL-03; 定型时间：; 产权所有： 天津赛思恩科技有限公司

淘宝店铺网址 https://shop267049597.taobao.com/?spm=a1z10.1-c.0.0.15c5752dQQYDYl

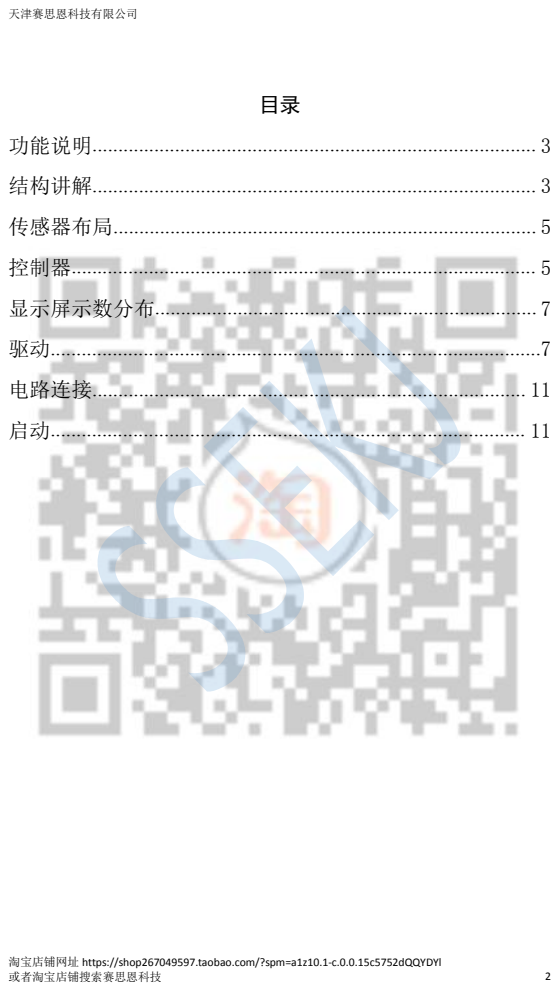
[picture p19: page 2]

### 功能说明

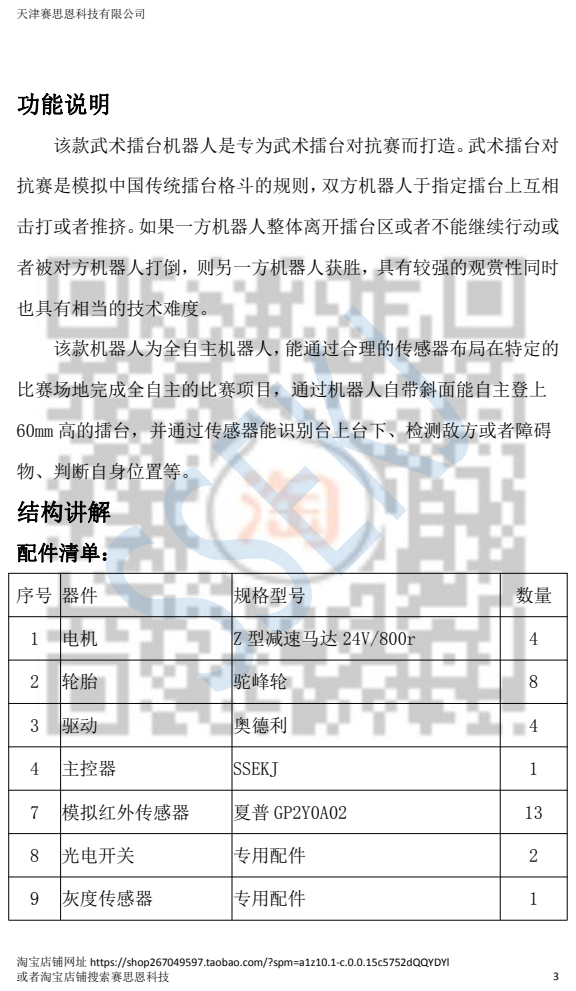
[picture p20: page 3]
该款武术擂台机器人是专为武术擂台对抗赛而打造。武术擂台对; 抗赛是模拟中国传统擂台格斗的规则，双方机器人于指定擂台上互相; 击打或者推挤。如果一方机器人整体离开擂台区或者不能继续行动或; 也具有相当的技术难度。; 该款机器人为全自主机器人，能通过合理的传感器布局在特定的; 比赛场地完成全自主的比赛项目，通过机器人自带斜面能自主登上; 物、判断自身位置等。 结构讲解; 配件清单：

者被对方机器人打倒，则另一方机器人获胜，具有较强的观赏性同时

60mm 高的擂台，并通过传感器能识别台上台下、检测敌方或者障碍

序号 | 器件 | 规格型号 | 数量

1 | 电机 | Z 型减速马达 24V/800r | 4

2 | 轮胎 | 驼峰轮 | 8

3 | 驱动 | 奥德利 | 4

4 | 主控器 | SSEKJ | 1

7 | 模拟红外传感器 | 夏普 GP2Y0A02 | 13

8 | 光电开关 | 专用配件 | 2

9 | 灰度传感器 | 专用配件 | 1

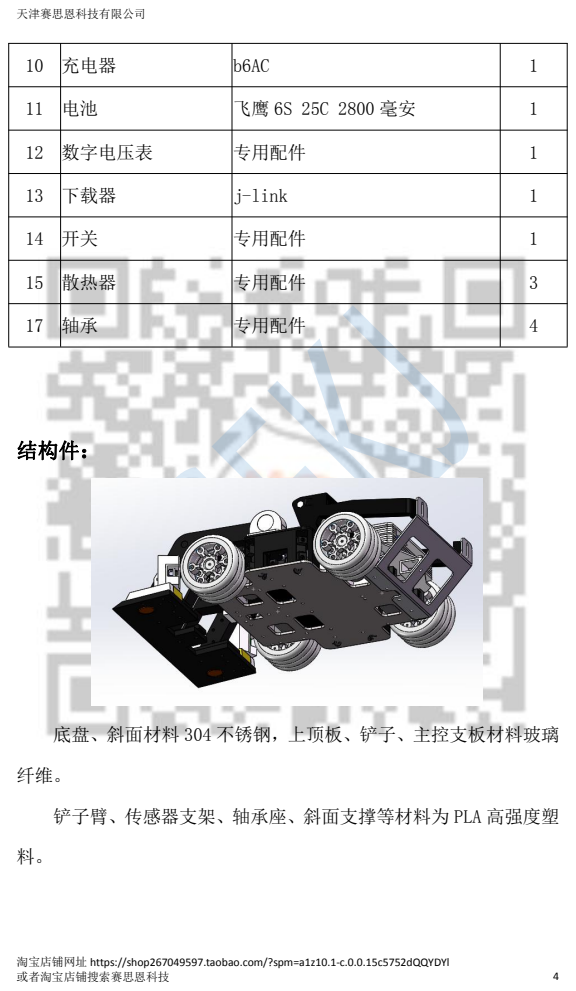
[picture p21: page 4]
结构件：

10 | 充电器 | b6AC | 1

12 | 数字电压表 | 专用配件 | 1

13 | 下载器 | j-link | 1

14 | 开关 | 专用配件 | 1

15 | 散热器 | 专用配件 | 3

17 | 轴承 | 专用配件 | 4

底盘、斜面材料 304 不锈钢，上顶板、铲子、主控支板材料玻璃

铲子臂、传感器支架、轴承座、斜面支撑等材料为 PLA 高强度塑

### 传感器布局

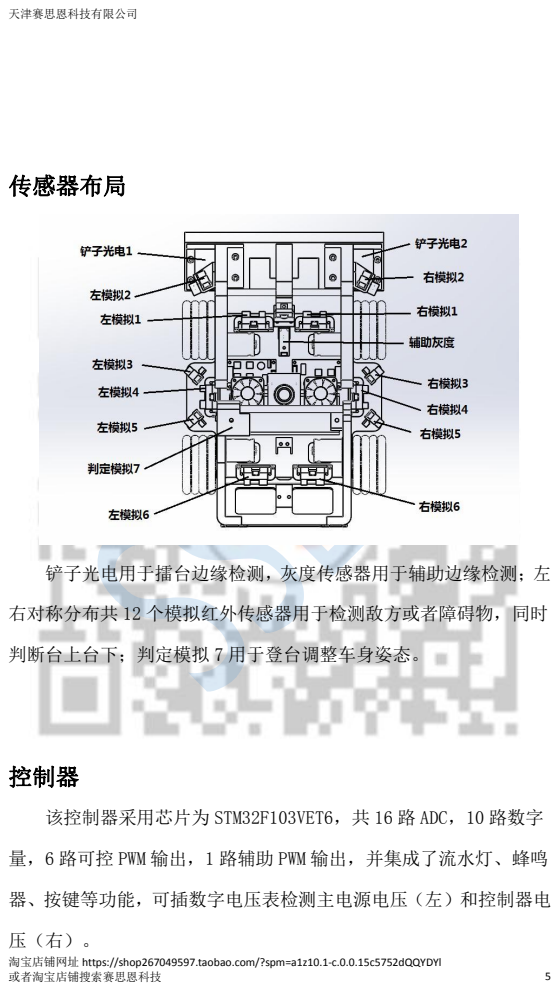
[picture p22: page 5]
铲子光电用于擂台边缘检测，灰度传感器用于辅助边缘检测；左

右对称分布共 12 个模拟红外传感器用于检测敌方或者障碍物，同时

判断台上台下；判定模拟 7 用于登台调整车身姿态。 控制器

该控制器采用芯片为 STM32F103VET6，共 16 路 ADC，10 路数字

量，6 路可控 PWM 输出，1 路辅助 PWM 输出，并集成了流水灯、蜂鸣

器、按键等功能，可插数字电压表检测主电源电压（左）和控制器电

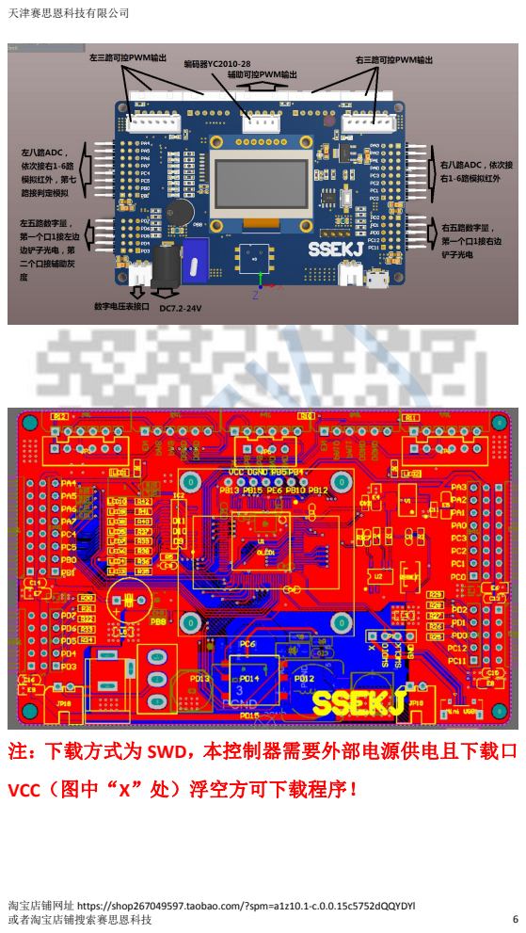
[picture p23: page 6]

注：下载方式为 SWD，本控制器需要外部电源供电且下载口

VCC（图中“X”处）浮空方可下载程序！

### 显示屏示数分布

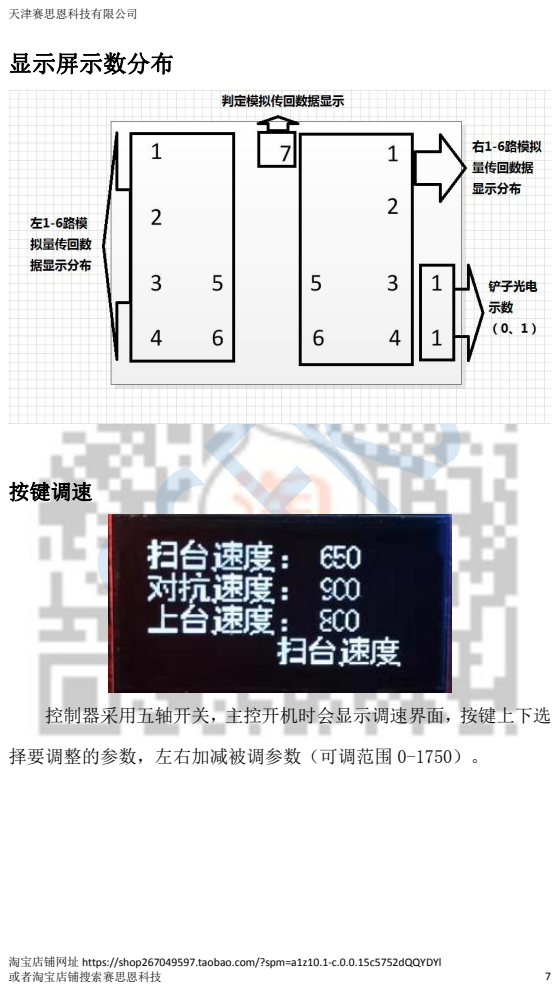
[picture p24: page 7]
按键调速

控制器采用五轴开关，主控开机时会显示调速界面，按键上下选

择要调整的参数，左右加减被调参数（可调范围 0-1750）。

驱动

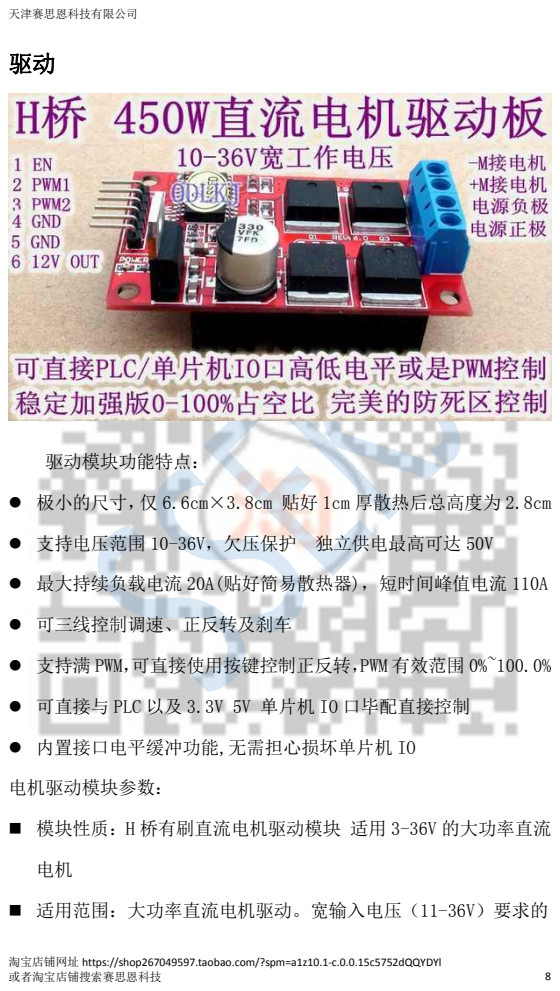
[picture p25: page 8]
驱动模块功能特点：; ● 可三线控制调速、正反转及刹车; 电机驱动模块参数：

● 极小的尺寸，仅 6.6cm×3.8cm 贴好 1cm 厚散热后总高度为 2.8cm

● 支持电压范围 10-36V，欠压保护 独立供电最高可达 50V

● 最大持续负载电流 20A(贴好简易散热器)，短时间峰值电流 110A

● 支持满 PWM，可直接使用按键控制正反转，PWM 有效范围 0%~100.0%

● 可直接与 PLC 以及 3.3V 5V 单片机 IO 口毕配直接控制

● 内置接口电平缓冲功能,无需担心损坏单片机 IO

■ 模块性质：H 桥有刷直流电机驱动模块 适用 3-36V 的大功率直流

■ 适用范围：大功率直流电机驱动。宽输入电压（11-36V）要求的

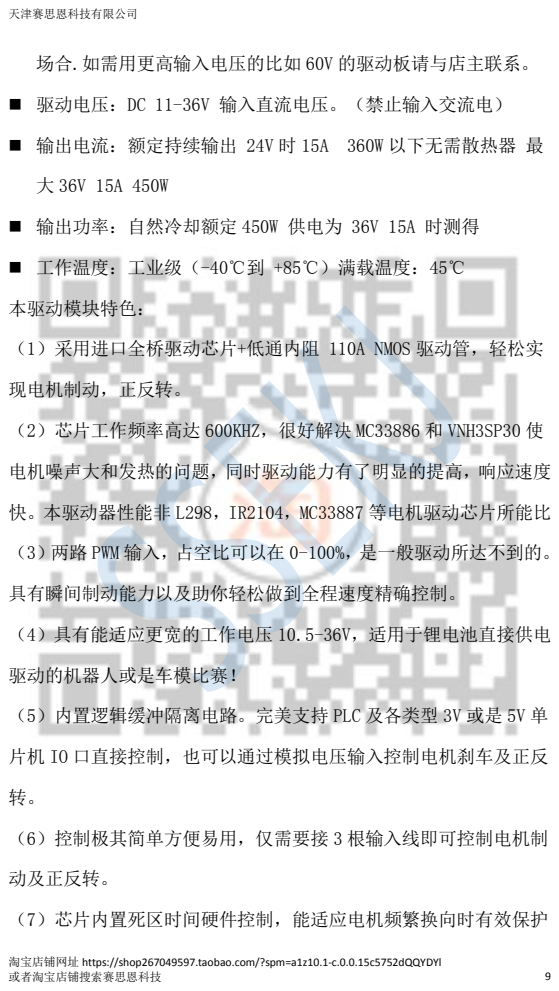
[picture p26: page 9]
本驱动模块特色：; 现电机制动，正反转。; （2）芯片工作频率高达 600KHZ，很好解决 MC33886 和 VNH3SP30 使; 快。本驱动器性能非 L298，IR2104，MC33887 等电机驱动芯片所能比; 具有瞬间制动能力以及助你轻松做到全程速度精确控制。; （4）具有能适应更宽的工作电压 10.5-36V，适用于锂电池直接供电; 驱动的机器人或是车模比赛！; 动及正反转。; （7）芯片内置死区时间硬件控制，能适应电机频繁换向时有效保护

场合.如需用更高输入电压的比如 60V 的驱动板请与店主联系。

■ 驱动电压：DC 11-36V 输入直流电压。（禁止输入交流电）

■ 输出电流：额定持续输出 24V 时 15A 360W 以下无需散热器 最

■ 输出功率：自然冷却额定 450W 供电为 36V 15A 时测得

■ 工作温度：工业级（-40℃到 +85℃）满载温度：45℃

（1）采用进口全桥驱动芯片+低通内阻 110A NMOS 驱动管，轻松实

电机噪声大和发热的问题，同时驱动能力有了明显的提高，响应速度

（3）两路 PWM 输入，占空比可以在 0-100%，是一般驱动所达不到的。

（5）内置逻辑缓冲隔离电路。完美支持 PLC 及各类型 3V 或是 5V 单

片机 IO 口直接控制，也可以通过模拟电压输入控制电机刹车及正反

（6）控制极其简单方便易用，仅需要接 3 根输入线即可控制电机制

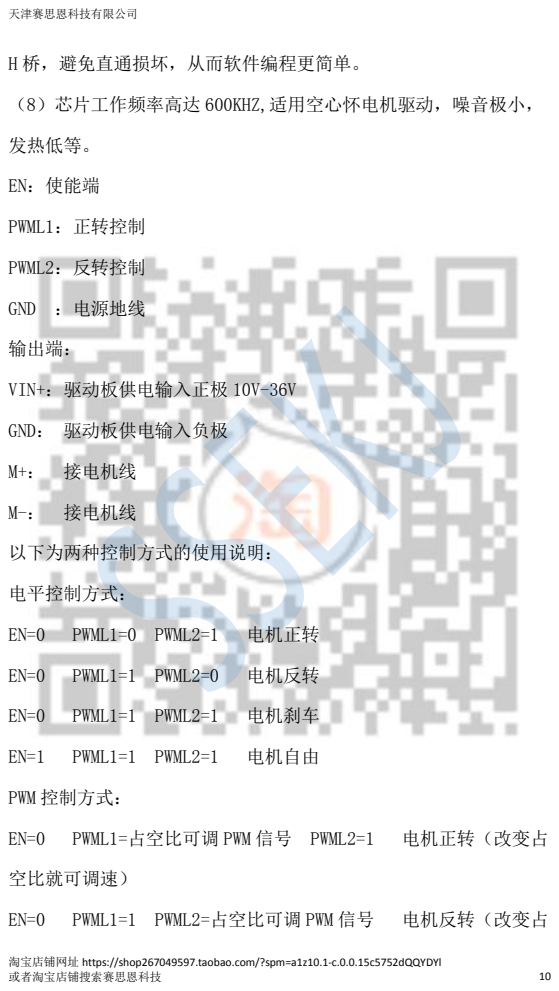
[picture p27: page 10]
H 桥，避免直通损坏，从而软件编程更简单。; 发热低等。; EN：使能端; PWML1：正转控制; PWML2：反转控制; GND ：电源地线; 输出端：; VIN+：驱动板供电输入正极 10V-36V; GND： 驱动板供电输入负极; M+： 接电机线; M-： 接电机线; 以下为两种控制方式的使用说明：; 电平控制方式：; PWML1=0 PWML2=1; 电机正转; PWML1=1 PWML2=0; 电机反转; PWML1=1 PWML2=1; 电机刹车; 电机自由; PWM 控制方式：; PWML1=占空比可调 PWM 信号 PWML2=1; 电机正转（改变占; 空比就可调速）; PWML1=1 PWML2=占空比可调 PWM 信号; 电机反转（改变占

（8）芯片工作频率高达 600KHZ,适用空心怀电机驱动，噪音极小，

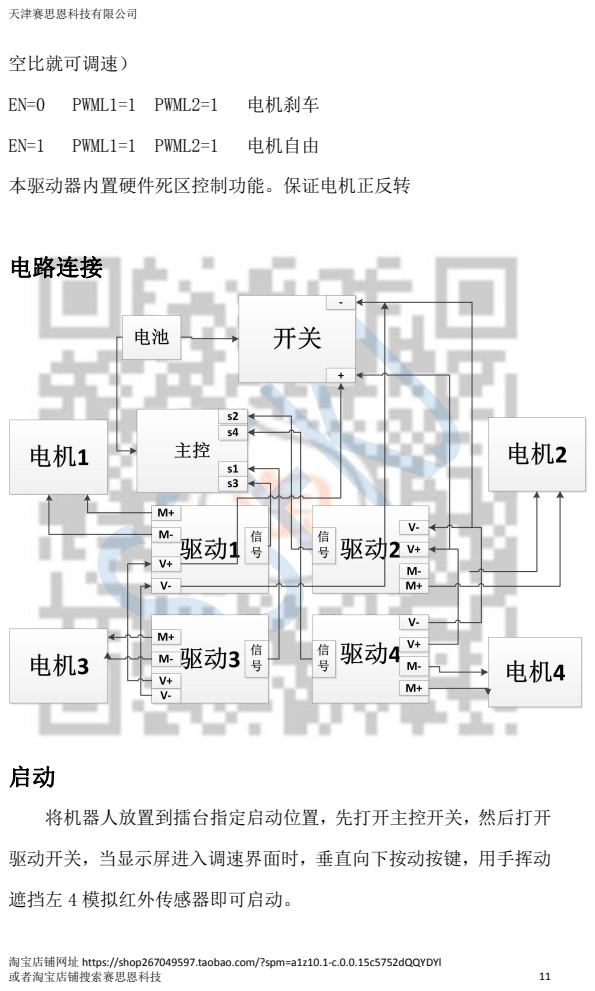
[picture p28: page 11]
空比就可调速）; PWML1=1 PWML2=1; 电机刹车; 电机自由; 本驱动器内置硬件死区控制功能。保证电机正反转; 电路连接; 遮挡左 4 模拟红外传感器即可启动。

将机器人放置到擂台指定启动位置，先打开主控开关，然后打开

驱动开关，当显示屏进入调速界面时，垂直向下按动按键，用手挥动

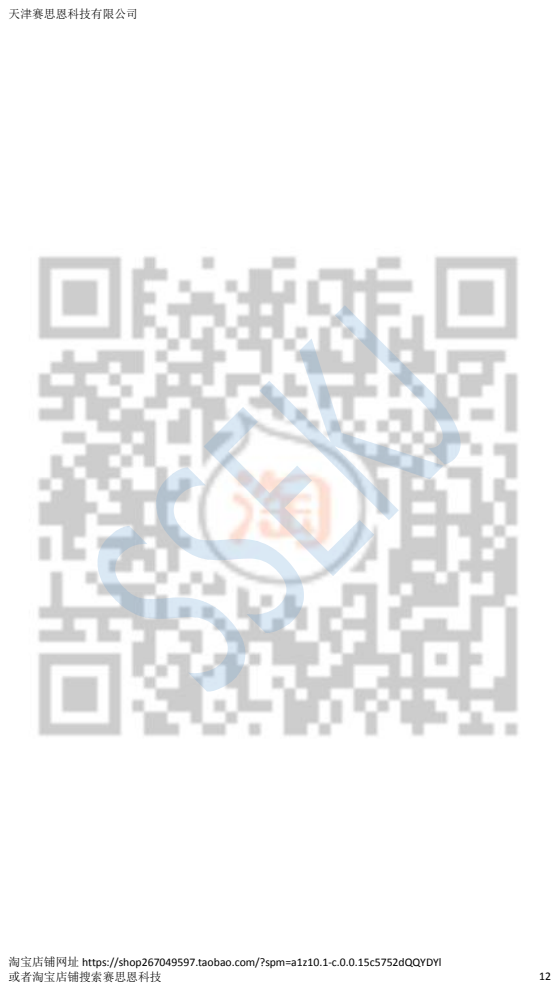
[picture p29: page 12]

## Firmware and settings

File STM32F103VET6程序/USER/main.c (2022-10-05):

#include "delay.h"
#include "sys.h"
#include "oled.h"
#include "pwm.h"
#include "delay.h"
#include "adc.h"
#include "move.h"
#include "scan.h"
#include "buzzer.h"
#include "dma.h"
#include "timer.h"
#define TEST 0   //1为测试，0为不测试
void understage_move(void);
void delay(int t);
void TIM3_IRQHandler(void);   //TIM3中断
void DMA1_Channel1_IRQHandler(void);
void bianyuanshibiex(void);
void check(void);
void show(void);
void set_num(void);
void understage_onstage_ide(void);
void data_filter(void);
void UP_stage(void);
u8 set_led(u8 a);
extern u32 GROUP;
extern unsigned char zheng_or_fan;
extern u32	TIM3CH1_CAPTURE_VAL;	//输入捕获值	 
extern int time;
u32 temp_z1=0,//左一
		temp_z2=0,
		temp_z3=0,
		temp_z4=0,
		temp_z5=0,
		temp_z6=0,
		temp_y1=0,
		temp_y2=0,
		temp_y3=0,
		temp_y4=0,
		temp_y5=0,
		temp_y6=0,
		temp_Qz=0,//前上
		temp_Hz=0,//后中
		temp_back_H=0		,
		THRE_VALUE =1300,
		front_value  = 1300,
		left_value = 1300,
		right_value = 1300,
		us_delay = 3000;

		
		
u8  mm1,//数字红外左
		mm2,//灰度中
		mm2last,
		mm3,//数字红外右
		mm4,
		key=0,
		avr_mm2=0,
		key_flag=0,//中间按键
		front_flag = 0,//前方有障碍物
		left_flag  = 0,
		right_flag = 0,
		back_flag  = 0,
		front_left_flag = 0,
		front_right_flag = 0,
		back_right_flag = 0,
		back_left_flag = 0,
		location_flag	 = 0,//擂台上下标志，0在擂台上，1在擂台下
		allaheadflag=0,
		backflag		=0,
		backflag1=0,
		ltxback=0,//还没用
		ltxahead=0,//还没用
		ltsbin=0,//还没用
		enemyflag=0,//
		except_left_flag = 0,
		except_right_flag = 0,
		except_front_flag = 0,
		except_back_flag = 0;
		
u32  yj=0,
		 zj=0,//前进标志位计数
		 ot=0;
		 
u16 value[15];
u8 chr[]="mm2",chr1[]="YT";
int x1=0,
		i,
		xj=0,
		kp=2,
		kd=1,
		lasttime=0,
		apwm=0,
		expectspeed=0,
		error=0,
		key_num=0,
		up_stage_delay=0,				//上台延时标志
		enemy_monitor=0,				//擂台上敌人监视
		understage_enemy = 0,  //擂台下有敌人
		circle=0;	
u32 check45_PWM=900,check90_PWM=900,check45_TIME=100,check90_TIME=200,checkback_PWM=700,checkback_TIME=200;  //check参数设置
 int main(void)
 {
	  
	delay_init();               //延时函数初始化	
  delay_ms(1000);	 
  delay_ms(1000);	 
	NVIC_Configuration(); 	    //设置NVIC中断分组2:2位抢占优先级，2位响应优先级 	LED_Init();			     //LED端口初始化
	BUZZER_GPIO_Config();		  	//
	OLED_Init();			          //初始化OLED	
	MYDMA_Config(DMA1_Channel1,(u32)&ADC1->DR,(u32)&value,15);//初始化DMA
	Adc_Init();               	//初始化ADC 
  TIM1_PWM_Init(1799,3);     //电机PWM频率=72000/(1799+1)=40Khz	
	TIM2_Int_Init(2499,143);                        //定时器	
	mm_scan_GPIO_Config();     //红外对管管脚初始化（普通IO输入）	 	 
	OLED_Clear();          //OLED 清零
	
		
	while(value[2]<THRE_VALUE)       //等待按键启动，key_flag是按键标志
	{
		set_num(); 
		OLED_ShowString(20,2,chr1);

	}
	delay_ms(100); 
	OLED_Clear();          //OLED 清零
	delay_ms(500);
	
	back(700,700)	;
	delay_ms(180)	; 
	stop();
	delay_ms(1000);
	
	back(1300,1300);
	delay_ms(800);
	left(1600);
	delay_ms(200);

	while(1)
				{
				#if TEST==1
					{
				//	backST(500);
				//backST(300);
			//			show();
			//			if(zhengorfan()==1) circle+=1;
			//			else if(zhengorfan()==2) circle-=1;
			//			//set_num();
			//mm2last=mm2;
					}  
				#else
					{
						show();                //显示参数
						understage_onstage_ide();//判断台上台下
						if(location_flag==0)
							bianyuanshibiex();     //擂台上边缘识别
						else
							understage_move();                //擂台下识别
						if(xj/160==1) {xj=0;}
						set_led(xj/20+1);
						if(mm2==0) {x1 = 1;}
						xj++;//与LED有关
						mm2last			 = mm2;
						allaheadflag = 0;	//前进标志位，与zj有关，
						ltxback		   = 0;	//没用
															//flag清零
					}
					#endif
			}
}
			 

/******************delay 改进*********************/


/**************************************************/
void delay(int t)
{
	int i;
	for(i=t/1000 ; i>0 ;i-- )
	{      
		delay_ms(1000);
	}
	delay_ms(t%1000);
}







/******************边缘改进*********************/


/**************************************************/
void bianyuanshibiex(void)//擂台上用定时器刷新数据，开启使能，关闭使能   寻台
{
	{	 
				if(value[6]> front_value ||value[5]> front_value)    // two sensor front find enemy 2  
				{	
					delay_us(us_delay);
					if(value[6]> front_value ||value[5]> front_value)
					{
								 if((mm_scan(GPIOD,GPIO_Pin_7)==1||mm_scan(GPIOD,GPIO_Pin_2)==1))
                 {
									 delay_us(us_delay);
									 if((mm_scan(GPIOD,GPIO_Pin_7)==1||mm_scan(GPIOD,GPIO_Pin_2)==1))
									 {
								    back(500,500);
										backflag=1;
									 }
								 }
								 else  
								 {
										  if(backflag==1)
											{
//												back(700,700);
//												delay_ms(300);//delay_ms(300)推棋子
//												if(yj==1)					
//												{
//													right(1600);			//
////																delay_ms(200);		//test
//												}												
//												else 
//													{
//														left(1600);		
//	//															delay_ms(200);		//test
//													}
//														delay_ms(100);
//														backflag=0;
												
														if(value[6]>2700||value[5]>2700) backflag=0;
														else 
														stop();
											 }
										  else
											{ 
												      allahead(1650);		
											}												
									}
						backflag1=0;	
					}																
				}
				else if((mm_scan(GPIOD,GPIO_Pin_7)==1||mm_scan(GPIOD,GPIO_Pin_2)==1)) 
				{
					delay_us(us_delay);
					if((mm_scan(GPIOD,GPIO_Pin_7)==1||mm_scan(GPIOD,GPIO_Pin_2)==1))
					{
						back(700,700);
						backflag1=1;
						xj=0;
						backflag=0;//   正常 边缘后退
					}
				}			
				else if(( value[3]>THRE_VALUE)||value[2]> left_value ||value[1]> left_value ||value[0]> left_value ) //one sensor  right and right back  find enemy  and right back   2   temp_ahead_right>1500 || temp_right>1500  ||  
				{
					delay_us(us_delay);
					if(( value[3]>THRE_VALUE)||value[2]> left_value ||value[1]> left_value ||value[0]> left_value)
					{
						left(1600);		//temp_z3~temp_z6
						yj=0;
						delay_ms(50);		//test	左敌 左转      speed 1500 delay 60
					}							
				}
				else if(( value[8]> right_value)||value[9]> right_value||value[10]> right_value||value[11]> right_value)  //one sensor left and left back find enemy 2    temp_left>1500 ||temp_back>1500 ||
				{
           delay_us(us_delay);
           if(( value[8]> right_value)||value[9]> right_value ||value[10]> right_value ||value[11]> right_value )
					 {
					    	right(1600);//temp_y3~temp_y6
								yj=1;
								delay_ms(50);		//test  右敌 右转  speed 1500 delay 60
					 }						 
				} 
				else 
				{
					backflag=0;
					if(backflag1==1)
					{									
						back(700,700);
						delay_ms(100); // 正常 增加后退距离
						if(yj==1)	
							{
								 right(1600);														
							}
						else 
						{
							 left(1600);														
						}
							delay_ms(100);			//正常 边缘左转										
							backflag1=0;
					}									
					else ahead(600);   // 正常 寻台速度 900/500
				}		
	}
}






///******************边缘改进*********************/           // 静止不动


///**************************************************/
//void bianyuanshibiex(void)//擂台上用定时器刷新数据，开启使能，关闭使能
//{
//				{	 
//							if(value[6]>THRE_VALUE||value[5]>THRE_VALUE )    // two sensor front find enemy 2  
//							{	
//								 if((mm_scan(GPIOD,GPIO_Pin_7)==1||mm_scan(GPIOD,GPIO_Pin_2)==1))  {back(500,500);backflag=1;}
//								 else  
//											{
//												if(backflag==1)
//													{
//														back(700,700);
//														delay_ms(200);//delay_ms(300)推棋子
////														if(yj==1)					
////															{
////																right(1600);			//
////																delay_ms(200);		//test
////															}												
////														else 
////															{
////																left(1600);		
////																delay_ms(200);		//test
////															}
////																delay_ms(150);
////																backflag=0;
//													 }
//											else		allahead(1600); //1600
//												allaheadflag=1;				
//											}
//								backflag1=0;																			
//							}
//				else if((mm_scan(GPIOD,GPIO_Pin_7)==1||mm_scan(GPIOD,GPIO_Pin_2)==1)) 
//							{
//									back(1300,1300);  backflag1=1;xj=0;backflag=0;//
//							}			
//				else if(( value[3]>THRE_VALUE)||value[2]>THRE_VALUE||value[1]>THRE_VALUE||value[0]>THRE_VALUE) //one sensor  right and right back  find enemy  and right back   2   temp_ahead_right>1500 || temp_right>1500  ||
//							{
//									left(1600);		//temp_z3~temp_z6
//									yj=0;
//									delay_ms(50);		//test								
//							}
//				else if(( value[8]>THRE_VALUE)||value[9]>THRE_VALUE||value[10]>THRE_VALUE||value[11]>THRE_VALUE)  //one sensor left and left back find enemy 2    temp_left>1500 ||temp_back>1500 ||
//							{ 
//									right(1600);//temp_y3~temp_y6
//									yj=1;
//									delay_ms(50);		//test
//							}
//				//
//				//
////				else if((value[6]>THRE_VALUE||value[5]>THRE_VALUE)&&(mm_scan(GPIOD,GPIO_Pin_7)==1||mm_scan(GPIOD,GPIO_Pin_2)==1))
////							{
////							   back(700,700);
////								 delay_ms(100);
////								 stop();
////								 delay_ms(50000);							
////							}
////				//
//				//
//				else 
//								{
//									backflag=0;
//									if(backflag1==1)
//											{											
//												//back(500,500);delay_ms(100);
//												if(yj==1)	
//													{
//														 right(1600);														
//													}
//												else 
//													{
//														 left(1600);														
//													}
//													delay_ms(150);			//边缘左转										
//													backflag1=0;
//											}									
//									else right(100);//ahead(1100);//back(1300,1300);delay_ms(200);
//								}							 
//				}
//}





/*****************位置识别************************/


/**************************************************/
/*****************位置识别************************/


/**************************************************/
void understage_onstage_ide()
{
	front_flag 	 			= 0;
	left_flag  	 			= 0;
	right_flag   			= 0;
	back_flag    			= 0;
	except_left_flag = 0;
	except_right_flag = 0;
	except_front_flag = 0;
	except_back_flag = 0;
	
	if(temp_z1>THRE_VALUE||temp_y1>THRE_VALUE)    // Left01 Right01
			front_flag 			 = 1;
	if( temp_z3>THRE_VALUE||temp_z4>THRE_VALUE||temp_z5>THRE_VALUE)  // Left02 Left03 Left04
			left_flag  			 = 1;
	if( temp_y3>THRE_VALUE||temp_y4>THRE_VALUE||temp_y5>THRE_VALUE)  // Right02 Right03 Right04
			right_flag 			 = 1;
	if( temp_z6>THRE_VALUE||temp_y6>THRE_VALUE) // Left05 Right05
			back_flag  			 = 1;
	if(front_flag == 1 && (back_flag == 1 || temp_z4>THRE_VALUE || temp_y4>THRE_VALUE))
		  except_front_flag = 1;
	if(back_flag == 1 && (front_flag == 1 || temp_z4>THRE_VALUE||temp_z3>THRE_VALUE || temp_y4>THRE_VALUE||temp_y3>THRE_VALUE))
		  except_back_flag = 1;
	if(left_flag == 1 && (right_flag == 1 || temp_y1>THRE_VALUE || temp_y6>THRE_VALUE))
		  except_left_flag = 1;
	if(right_flag == 1 && (left_flag == 1 || temp_z1>THRE_VALUE || temp_z6>THRE_VALUE))
		  except_right_flag = 1;
	
	if(except_front_flag == 1 ||  except_back_flag == 1 || except_left_flag == 1 || except_right_flag == 1)
			location_flag 	 = 1;				//擂台下
	else
			location_flag 	 = 0;					//擂台上
}


/****************擂台下程序**************************/


/**************************************************/
void understage_move()
{		
			if(temp_z1>THRE_VALUE&&temp_y1>THRE_VALUE&&temp_y6>THRE_VALUE&&temp_z6>THRE_VALUE&&(temp_z4<THRE_VALUE||temp_y4<THRE_VALUE)&&temp_back_H<THRE_VALUE&&location_flag==1)		//if(front_flag==1&&back_flag==1&&temp_Qz>1300)test
				{				                                           // 后退标准位置
						up_stage_delay += 1;
						delay_ms(50);
						if(up_stage_delay>3)		
						{							
							  ahead(500);
								delay_ms(1000);	//撞墙
								 UP_stage();
									x1=0;
									up_stage_delay = 0;		
						}				
         }
				else if((temp_z1>1700||temp_y1>1700)&&temp_y3>1700&&temp_y4>1700)  
					{
						ahead(400);
						ltxback=1;
					}
		      else if((temp_z1>1700||temp_y1>1700)&&temp_z3>1700&&temp_z4>1700)   
					{
						ahead(400);
						ltxback=2;
						
					}
				else
				{
					if(value[5]>3000||value[6]>3000)
						back(350,350);
					else 	
						right(400);
				}		
			
			if(ltxback==1||ltxback==2) 
				zj++;
			else 
				zj=0;
			
			if(zj>100) 
				{
			   if(ltxback==2)
				 {
					 back(700,700);
					 delay_ms(100);
					 
					 while(value[5]>500&&value[6]>500)
						 right(400);
					 
					 ahead(700);
					 delay_ms(1000);
					 left(700);
					 delay_ms(300);
						zj=0;
				 }
				 else if(ltxback==1)
				 {
					back(700,700);
					 delay_ms(100); 
					 
					while(value[5]>500&&value[6]>500) 
						left(400);
					
					 ahead(700);
					 delay_ms(1000);
					 right(700);
					 delay_ms(300);
					 zj=0;
				 }
			 }			
}											
							

/****************显示与检测**************************/



/*********************************************/
void show()
{
    
	
		data_filter();
    mm1=mm_scan(GPIOD,GPIO_Pin_7);// 
		mm2=mm_scan(GPIOD,GPIO_Pin_6);                   
	 	mm3=mm_scan(GPIOD,GPIO_Pin_2);                  
		mm4=mm_scan(GPIOD,GPIO_Pin_1);                    
	                  
	if(temp_z1>1300)	 OLED_ShowNum(0,0,temp_z1,4,12);
	else OLED_ShowNum(0,0,0,4,12);
	if(temp_z3>1300)	 OLED_ShowNum(0,4,temp_z3,4,12);
	else OLED_ShowNum(0,4,0,4,12);
	if(temp_z4>1300)	 OLED_ShowNum(0,6,temp_z4,4,12);
	else OLED_ShowNum(0,6,0,4,12);
	if(temp_z5>1300)   OLED_ShowNum(26,2,temp_z5,4,12);
	else OLED_ShowNum(26,2,0,4,12);
	if(temp_z6>1300)	 OLED_ShowNum(26,4, temp_z6,4,12);
	else OLED_ShowNum(26,4, 0,4,12);
	if(temp_y1>1300)	 OLED_ShowNum(78,0,temp_y1,4,12);
	else OLED_ShowNum(78,0,0,4,12);
 	if(temp_y3>1300)  OLED_ShowNum(78,4,temp_y3,4,12);
	else OLED_ShowNum(78,4,0,4,12);
	if(temp_y4>1300)  OLED_ShowNum(78,6,temp_y4,4,12);
	else OLED_ShowNum(78,6,0,4,12);
	if(temp_y5>1300)  OLED_ShowNum(52,2,temp_y5,4,12); 
	else OLED_ShowNum(52,2,0,4,12); 
	if(temp_y6>1300)		OLED_ShowNum(52,4,temp_y6,4,12); 	
	else OLED_ShowNum(52,4,0,4,12);
	if(temp_back_H>1300)		OLED_ShowNum(39,0,temp_back_H,4,12); 
	else 	OLED_ShowNum(39,0,0,4,12); 
		OLED_ShowNum(104,0,mm1,1,5); 
		OLED_ShowNum(104,2,mm3,1,5); 
		OLED_ShowNum(104,4,location_flag,1,5);
}

 
char huodejianzhi()
{ //1 left   2 right   3 up    4 down   5 mid
	u8 key_l=0,key_r=0,key_up=0,key_down=0,key_mid=0;
	key_l=key_get(GPIOC,GPIO_Pin_6);      //d13
	key_r=key_get(GPIOD,GPIO_Pin_13);     //d12
	key_up=key_get(GPIOD,GPIO_Pin_12);     //c6
	key_down=key_get(GPIOD,GPIO_Pin_14);   //d15
	key_mid=key_get(GPIOD,GPIO_Pin_15);    //d14
	//OLED_Clear()  	;
	/* OLED_ShowNum(0,2,key_l,4,12);
	 OLED_ShowNum(52,2,key_r,4,12);
	 OLED_ShowNum(26,0,key_up,4,12);
	 OLED_ShowNum(26,4,key_down,4,12);
	 OLED_ShowNum(26,2,key_mid,4,12);*/
	
   if(key_l ==  1)   //left
  {
     key=1;
	}



if(key_r ==  1)   //right
{ 
{key=2;
}
}



if(key_up ==  1)   //up
{ 
{key=3;
}
}





if(key_down ==  1) //down
{
  
  {key=4;
}
}
 
if(key_mid ==  1)   //mid
{
  
  {key=5;
}
}

return key;		}


void set_num()
 {
		switch(huodejianzhi())//the value of key
			{
			 case 5:   //mid
							{
								key=0;
								delay_ms(150);
								if(key_flag==1)
										{
											key_flag=0;
										}
								else if(key_flag==0)
										{
											key_flag=1;
										}
								delay_ms(150);
								//xj-=1;
								} break;   
		default: break;
		case 4:   //down
			{
			key=0;
			 delay_ms(120);
			 xj-=1;
				delay_ms(120);

		 
			} break;

		case 3:  //up
			{
			key=0;
			 delay_ms(120);
			xj+=1;
			 delay_ms(120);
			}break;

		 case 2:  //right
						if(key_num==0)
					{
					
				 key=0;
					 delay_ms(120);
					 xj+=50; 
					 delay_ms(120);
					}
        break;


case 1: //left
         if(key_num==0)
      {
      
     key=0;
       delay_ms(120);
       xj-=50; 
       delay_ms(120);
      }
         break;
}

 
}

u8 set_led(u8 a)

{
		switch(a)
		{
			case 1:
			GPIO_ResetBits(GPIOD,GPIO_Pin_11);   //a
			GPIO_ResetBits(GPIOD,GPIO_Pin_10);    //b
			GPIO_ResetBits(GPIOD,GPIO_Pin_9);    //c
			break;  
			case 2:
			GPIO_SetBits(GPIOD,GPIO_Pin_11);   //a
			GPIO_ResetBits(GPIOD,GPIO_Pin_10);    //b
			GPIO_ResetBits(GPIOD,GPIO_Pin_9);    //c
			break;  
			case 3:
			GPIO_ResetBits(GPIOD,GPIO_Pin_11);   //a
			GPIO_SetBits(GPIOD,GPIO_Pin_10);    //b
			GPIO_ResetBits(GPIOD,GPIO_Pin_9);    //c
			break;  
			case 4:
			GPIO_SetBits(GPIOD,GPIO_Pin_11);   //a
			GPIO_SetBits(GPIOD,GPIO_Pin_10);    //b
			GPIO_ResetBits(GPIOD,GPIO_Pin_9);    //c
			break;  
			case 5:
			GPIO_ResetBits(GPIOD,GPIO_Pin_11);   //a
			GPIO_ResetBits(GPIOD,GPIO_Pin_10);    //b
			GPIO_SetBits(GPIOD,GPIO_Pin_9);    //c
			break;  
			case 6:
			GPIO_SetBits(GPIOD,GPIO_Pin_11);   //a
			GPIO_ResetBits(GPIOD,GPIO_Pin_10);    //b
			GPIO_SetBits(GPIOD,GPIO_Pin_9);    //c
			break;  
			case 7:
			GPIO_ResetBits(GPIOD,GPIO_Pin_11);   //a
			GPIO_SetBits(GPIOD,GPIO_Pin_10);    //b
			GPIO_SetBits(GPIOD,GPIO_Pin_9);    //c
			break;  
			case 8:
			GPIO_SetBits(GPIOD,GPIO_Pin_11);   //a
			GPIO_SetBits(GPIOD,GPIO_Pin_10);    //b
			GPIO_SetBits(GPIOD,GPIO_Pin_9);    //c
			break;  
			
		}
		return 0;
}


void data_filter(void)
{
		u8 i;
    temp_z1=0;
	  temp_z2=0;
    temp_z3=0;
	  temp_z4=0;
	  temp_z5=0;   
	  temp_z6=0;//      
    temp_y1=0;//     
		temp_y2=0;//  
		temp_y3=0;//   
	  temp_y4=0;//  
	  temp_y5=0;// 
	  temp_y6=0;//
	  temp_Hz=0;
		temp_back_H=0;

		for(i=0;i<2;i++)
				{
					temp_z1=(value[5]>>1)+temp_z1;//      
					temp_z3=(value[3]>>1)+temp_z3;//   
					temp_z4=(value[2]>>1)+temp_z4;//    
					temp_z5=(value[1]>>1)+temp_z5;//     
					temp_z6=(value[0]>>1)+temp_z6;//      
					temp_y1=(value[6]>>1)+temp_y1;//      
					temp_y3=(value[8]>>1)+temp_y3;//   
					temp_y4=(value[9]>>1)+temp_y4;//  
					temp_y5=(value[10]>>1)+temp_y5;// 
					temp_y6=(value[11]>>1)+temp_y6;//
					temp_back_H=(value[14]>>1)+temp_back_H;//
				}
}


void UP_stage()
{	
	back(1300,1300);
	delay_ms(800);
}

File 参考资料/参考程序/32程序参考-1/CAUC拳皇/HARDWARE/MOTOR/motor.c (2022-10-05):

//////////////////////////////////////////////////////////////////////////////////
//本程序仅供学习使用，未经作者许可，不得用于其它任何用途
//
//电机驱动代码
//编者：徐天泽
//版本：V1.0
//修改日期:2018/10/02
//
//组名：CAUC拳皇
//组长：史葆青
//组员：年  哲 葛  畅 徐天泽 郭景仁
//////////////////////////////////////////////////////////////////////////////////
#include "motor.h"

/** 
	* @brief	所有电机初始化
	* @since	v1.0
	* @note		电机PWM频率=72000/(1799+1)=40Khz
	*/
void MOTOR_Init(void)
{
	TIM1_PWM_Init(1799,0);
	TIM4_PWM_Init(1799,0);
}



/** 
	* @brief	运动电机初始化
	* @since	v1.0
	*/
void TIM1_PWM_Init(u16 arr,u16 psc)
{  
	
 	GPIO_InitTypeDef GPIO_InitStructure;
	TIM_TimeBaseInitTypeDef  TIM_TimeBaseStructure;
	TIM_OCInitTypeDef  TIM_OCInitStructure;

	RCC_APB2PeriphClockCmd(RCC_APB2Periph_TIM1, ENABLE);
 	RCC_APB2PeriphClockCmd(RCC_APB2Periph_GPIOA , ENABLE);
	                                                                     	
	GPIO_InitStructure.GPIO_Pin = GPIO_Pin_8|GPIO_Pin_9|GPIO_Pin_10|GPIO_Pin_11;
	GPIO_InitStructure.GPIO_Mode = GPIO_Mode_AF_PP;
	GPIO_InitStructure.GPIO_Speed = GPIO_Speed_50MHz;
	GPIO_Init(GPIOA, &GPIO_InitStructure);

	TIM_DeInit(TIM1); 

	TIM_TimeBaseStructure.TIM_Period = arr;
	TIM_TimeBaseStructure.TIM_Prescaler =psc;
	TIM_TimeBaseStructure.TIM_ClockDivision = 0; 
	TIM_TimeBaseStructure.TIM_CounterMode = TIM_CounterMode_Up;
	TIM_TimeBaseInit(TIM1, &TIM_TimeBaseStructure);

 
	TIM_OCInitStructure.TIM_OCMode = TIM_OCMode_PWM2;
	TIM_OCInitStructure.TIM_OutputState = TIM_OutputState_Enable; 
	TIM_OCInitStructure.TIM_Pulse = 0;
	TIM_OCInitStructure.TIM_OCPolarity = TIM_OCPolarity_High; 
	TIM_OC1Init(TIM1, &TIM_OCInitStructure); 
	TIM_OC2Init(TIM1, &TIM_OCInitStructure); 
	TIM_OC3Init(TIM1, &TIM_OCInitStructure);
	TIM_OC4Init(TIM1, &TIM_OCInitStructure);

	TIM_CtrlPWMOutputs(TIM1,ENABLE);

	TIM_OC1PreloadConfig(TIM1, TIM_OCPreload_Enable);
	TIM_OC2PreloadConfig(TIM1, TIM_OCPreload_Enable); 
	TIM_OC3PreloadConfig(TIM1, TIM_OCPreload_Enable);
	TIM_OC4PreloadConfig(TIM1, TIM_OCPreload_Enable);
	
	TIM_ARRPreloadConfig(TIM1, ENABLE);
	
	TIM_Cmd(TIM1, ENABLE);
}



/** 
	* @brief	上台电机初始化
	* @since	v3.0
	*/
void TIM4_PWM_Init(u16 arr,u16 psc)
{  
	
 	GPIO_InitTypeDef GPIO_InitStructure;
	TIM_TimeBaseInitTypeDef  TIM_TimeBaseStructure;
	TIM_OCInitTypeDef  TIM_OCInitStructure;

	RCC_APB1PeriphClockCmd(RCC_APB1Periph_TIM4  , ENABLE);
 	RCC_APB2PeriphClockCmd(RCC_APB2Periph_GPIOB , ENABLE);
	                                                                     	
	GPIO_InitStructure.GPIO_Pin = GPIO_Pin_8|GPIO_Pin_9;
	GPIO_InitStructure.GPIO_Mode = GPIO_Mode_AF_PP;
	GPIO_InitStructure.GPIO_Speed = GPIO_Speed_50MHz;
	GPIO_Init(GPIOB, &GPIO_InitStructure);

	TIM_DeInit(TIM4); 

	TIM_TimeBaseStructure.TIM_Period = arr;
	TIM_TimeBaseStructure.TIM_Prescaler =psc;
	TIM_TimeBaseStructure.TIM_ClockDivision = 0; 
	TIM_TimeBaseStructure.TIM_CounterMode = TIM_CounterMode_Up;
	TIM_TimeBaseInit(TIM4, &TIM_TimeBaseStructure);

 
	TIM_OCInitStructure.TIM_OCMode = TIM_OCMode_PWM2;
	TIM_OCInitStructure.TIM_OutputState = TIM_OutputState_Enable; 
	TIM_OCInitStructure.TIM_Pulse = 0;
	TIM_OCInitStructure.TIM_OCPolarity = TIM_OCPolarity_Low; 
	TIM_OC3Init(TIM4, &TIM_OCInitStructure);
	TIM_OC4Init(TIM4, &TIM_OCInitStructure);

	TIM_CtrlPWMOutputs(TIM4,ENABLE);

	TIM_OC3PreloadConfig(TIM4, TIM_OCPreload_Enable);
	TIM_OC4PreloadConfig(TIM4, TIM_OCPreload_Enable);
	
	TIM_ARRPreloadConfig(TIM4, ENABLE);
	
	TIM_Cmd(TIM4, ENABLE);
}



/** 
	* @brief	登台
	* @param	pwm_value_x		登台电机PWM比较值
	* @param	pwm_value_y		登台电机PWM比较值
	* @param	delay_time_x	冲刺电机运转时间
	* @param	delay_time_y	登台电机运转时间
	* @since	v3.0
	*/
void CAR_Jump(u16 pwm_value_x,u16 pwm_value_y,u16 delay_time_x,u16 delay_time_y)
{
	if(pwm_value_x > MAX_PWM)
		pwm_value_x = MAX_PWM;
	if(pwm_value_y > MAX_PWM)
		pwm_value_y = MAX_PWM;
	if(delay_time_x != 0)
	{
		TIM1->CCR1 = pwm_value_x;
		TIM1->CCR4 = pwm_value_x;
		delay_ms(delay_time_x);
	}
	TIM4->CCR3 = pwm_value_y;
	while(!EYE3_JP);
	delay_ms(10);
	while(EYE3_JP);
	TIM4->CCR3 = 0;
	delay_ms(delay_time_y);
	TIM1->CCR1 = 0;
	TIM1->CCR4 = 0;
}



/** 
	* @brief	刹车
	* @since	v1.0
	*/

void CAR_Stop()
{
	TIM1->CCR1 = 0;
	TIM1->CCR2 = 0;
	TIM1->CCR3 = 0;
	TIM1->CCR4 = 0;
}



/** 
	* @brief	车辆运动
	* @param	direction		运动方向
	* @param	pwm_value		PWM比较值
	* @since	v1.0
	*/
void CAR_Move(u8 direction,u16 pwm_value)
{
	if(pwm_value > MAX_PWM)
		pwm_value = MAX_PWM;
	switch(direction)
	{
		case FORWORD:
			TIM1->CCR1 = pwm_value;
			TIM1->CCR2 = 0;
			TIM1->CCR3 = 0;
			TIM1->CCR4 = pwm_value;
			break;
		case BACKWORD:
			TIM1->CCR1 = 0;
			TIM1->CCR2 = pwm_value;
			TIM1->CCR3 = pwm_value;
			TIM1->CCR4 = 0;
			break;
		case RIGHT:
			TIM1->CCR1 = pwm_value;
			TIM1->CCR2 = 0;
			TIM1->CCR3 = pwm_value;
			TIM1->CCR4 = 0;
			break;
		case LEFT:
			TIM1->CCR1 = 0;
			TIM1->CCR2 = pwm_value;
			TIM1->CCR3 = 0;
			TIM1->CCR4 = pwm_value;
			break;
		case STOP:
			TIM1->CCR1 = 0;
			TIM1->CCR2 = 0;
			TIM1->CCR3 = 0;
			TIM1->CCR4 = 0;
		default: 
			TIM1->CCR1 = pwm_value;
			TIM1->CCR2 = 0;
			TIM1->CCR3 = 0;
			TIM1->CCR4 = pwm_value;
	}
}

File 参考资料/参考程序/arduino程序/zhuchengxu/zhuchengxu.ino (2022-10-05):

//#include <IRremote.h>
//#include <Servo.h>
//Servo myservo1;  //头
//Servo myservo2;  //左手
//Servo myservo3;  //右手

int IR_hi=0;
int IR_forward1;
int IR_forward2;
int IR_left1;
int IR_left2;
int IR_right1;
int IR_right2;
int IR_backward1;
int IR_backward2;
int IR_cliff1;
int IR_cliff2;
int flag=0;

int speed_fast = 200;      //冲撞
int speed_normal = 100;    //正常
int speed_turn = 180;     //转弯
void setup()                                                                                                                
{

// myservo1.attach(A0);
// myservo2.attach(A1);
// myservo3.attach(A3);
 
  pinMode(A2,INPUT);     //红外
  pinMode(10,OUTPUT);    // P2
  pinMode(11,OUTPUT);    //D2
  pinMode(12,OUTPUT);    //P1
  pinMode(13,OUTPUT);    //D1

  pinMode(31,INPUT);//定义红外的接口
  pinMode(33,INPUT);
  pinMode(35,INPUT);
  pinMode(37,INPUT);
  pinMode(39,INPUT);
  pinMode(41,INPUT);
  pinMode(43,INPUT);
  pinMode(45,INPUT);
  pinMode(47,INPUT);
  pinMode(49,INPUT);

  digitalWrite(31,HIGH);   
  digitalWrite(33,HIGH);
  digitalWrite(35,HIGH);
  digitalWrite(37,HIGH);   
  digitalWrite(39,LOW);  //悬崖
  digitalWrite(41,HIGH);
  digitalWrite(43,HIGH);
  digitalWrite(45,LOW);  //悬崖
  digitalWrite(47,HIGH);
  digitalWrite(49,HIGH);
                       
  }
void loop()
{
  IR_forward1  = digitalRead(41);
  IR_forward2  = digitalRead(43); 
  IR_left1     = digitalRead(31);
  IR_left2     = digitalRead(47);
  IR_right1    = digitalRead(33);
  IR_right2    = digitalRead(49);
  IR_backward1 = digitalRead(35);
  IR_backward2 = digitalRead(37);
  IR_cliff1    = digitalRead(39);
  IR_cliff2    = digitalRead(45); 
 //stop(20);
//while(1); 
    
      if((IR_forward1 == LOW) ||  (IR_forward2 == LOW))    //forward straight  扫到障碍物 前红外亮 低电平
      {
        move_forward(speed_fast,speed_fast);
      }

      if((IR_forward1 == HIGH) && (IR_forward2 == HIGH))
        {
           move_forward(speed_normal,speed_normal);
        }
      if((IR_left1 == LOW) ||  (IR_left2 == LOW))    //forward straight
      {
        move_leftward(speed_turn,speed_turn,300);
      }

      if((IR_right1 == LOW) ||  (IR_right2 == LOW))    //forward straight
      {
        move_rightward(speed_turn,speed_turn,300);
      }

        
        
      if((IR_cliff1 == HIGH))    //deep cliff left
      {
        stop(20);
        move_backward(120,120,200);
        stop(40);
        move_rightward(speed_turn,speed_turn,300);    
      }
      
      if((IR_cliff2 == HIGH))    //deep cliff right
      {
         stop(20);
        move_backward(120,120,200);
         stop(40);
        move_leftward(speed_turn,speed_turn,300);       
      }
      if((IR_cliff1 == HIGH) && (IR_cliff2 == HIGH))    //deep cliff left  both
      {
         stop(20);
        move_backward(120,120,200);
         stop(40);
        move_rightward(speed_turn,speed_turn,300);    
      }
      if(((IR_left1 == LOW) ||(IR_left2 == LOW)) && ((IR_cliff1 == HIGH) && (IR_cliff2 == LOW)))
       {
        stop(20);
        move_backward(80,80,190);
         stop(40);
         move_rightward(speed_turn,speed_turn,170); 
       }
      if(((IR_left1 == LOW) ||(IR_left2 == LOW)) && ((IR_cliff1 == LOW) && (IR_cliff2 == HIGH)))
      {
        stop(20);
        move_backward(80,80,190);
         stop(40);
         move_leftward(speed_turn,speed_turn,170); 
       }
      
      if(((IR_right1 == LOW) || (IR_right2 == LOW)) && ((IR_cliff1 == HIGH) && (IR_cliff2 == LOW)))
      {
        stop(20);
        move_backward(80,80,190);
         stop(40);
        move_rightward(speed_turn,speed_turn,170); 
       }
      if(((IR_right1 == LOW) || (IR_right2 == LOW)) && ((IR_cliff1 == LOW) && (IR_cliff2 == HIGH)))
      {
        stop(20);
        move_backward(80,80,190);
         stop(40);
        move_leftward(speed_turn,speed_turn,170); 
       }
        
      if((IR_backward1 == LOW) ||(IR_backward2 == LOW))
      {
        move_rightward(200,200,400); 
       }
}
    


   

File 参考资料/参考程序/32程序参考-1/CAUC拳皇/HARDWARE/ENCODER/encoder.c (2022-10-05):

//////////////////////////////////////////////////////////////////////////////////
//本程序仅供学习使用，未经作者许可，不得用于其它任何用途
//
//编码器驱动代码
//编者：徐天泽
//版本：V1.0
//修改日期:2018/10/02
//
//组名：CAUC拳皇
//组长：史葆青
//组员：年  哲 葛  畅 徐天泽 郭景仁
//////////////////////////////////////////////////////////////////////////////////
#include "encoder.h"

/** 
	* @brief	初始化编码器
	* @since	v1.0
	*/
void ENCODER_Init()
{
  GPIO_InitTypeDef GPIO_InitStructure;
  TIM_TimeBaseInitTypeDef TIM_TimeBaseStructure;
  TIM_ICInitTypeDef TIM_ICInitStructure;      

	RCC_APB1PeriphClockCmd(RCC_APB1Periph_TIM3,ENABLE);
 	RCC_APB2PeriphClockCmd(RCC_APB2Periph_GPIOB|RCC_APB2Periph_AFIO,ENABLE);
	
  GPIO_AFIODeInit();	                                                                     	
	GPIO_PinRemapConfig(GPIO_PartialRemap_TIM3, ENABLE);
	GPIO_InitStructure.GPIO_Pin 	= GPIO_Pin_4 |GPIO_Pin_5;
	GPIO_InitStructure.GPIO_Mode 	= GPIO_Mode_IN_FLOATING;
	GPIO_InitStructure.GPIO_Speed = GPIO_Speed_50MHz;
	GPIO_Init(GPIOB, &GPIO_InitStructure);
	
	TIM_DeInit(TIM3);
	TIM_TimeBaseStructInit(&TIM_TimeBaseStructure);
	TIM_TimeBaseStructure.TIM_Period 				= 359*4;
	TIM_TimeBaseStructure.TIM_Prescaler 		= 0; 
	TIM_TimeBaseStructure.TIM_ClockDivision =	TIM_CKD_DIV1 ; 
	TIM_TimeBaseStructure.TIM_CounterMode		= TIM_CounterMode_Up;
	TIM_TimeBaseInit(TIM3, &TIM_TimeBaseStructure);

	TIM_EncoderInterfaceConfig(TIM3, TIM_EncoderMode_TI12, TIM_ICPolarity_BothEdge, TIM_ICPolarity_BothEdge);
	TIM_ICStructInit(&TIM_ICInitStructure);
	TIM_ICInitStructure.TIM_ICFilter = 6;
	TIM_ICInit(TIM3, &TIM_ICInitStructure);

	TIM_ClearFlag(TIM3, TIM_FLAG_Update);
	TIM_ITConfig(TIM3, TIM_IT_Update, ENABLE);
	
	TIM3->CNT = 0;

	TIM_Cmd(TIM3, ENABLE);
}



/** 
	* @brief	读取编码器读数
	* @return	读取到的数值
	* @since	v1.0
	*/
u16 ENCODER_Read()
{
	u16 temp=TIM3->CNT/4;
	TIM3->CNT=0;
	return temp>179?359-temp:temp;
}



/** 
	* @brief	定时器3中断服务函数
	* @since	v1.0
	*/
void TIM3_IRQHandler(void)
{                                   
	if(TIM3->SR&0X0001){}                 
	TIM3->SR&=~(1<<0);
}
